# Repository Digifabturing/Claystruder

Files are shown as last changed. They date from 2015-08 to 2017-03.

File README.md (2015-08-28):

# Claystruder

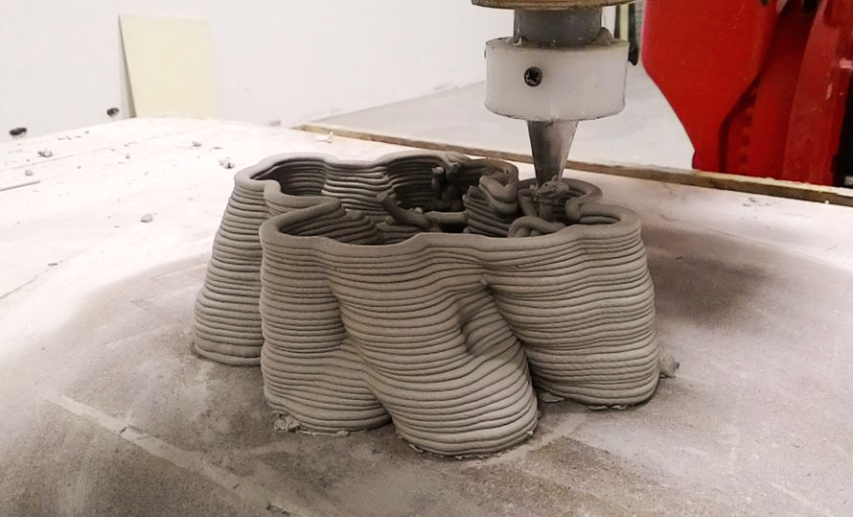
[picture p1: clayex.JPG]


### Introduction:

The Claystruder project is part of the digifabTuring research, that are a research
cluster focused about digital fabrication + robotic automation and material research
applied in the field of architecture, interaction design and art.
digifabTuring rises from a collaboration between several partners: Fablab Torino,
Officine Arduino, Co-de-iT with COMAU and Toolbox Coworking.

We have developed an hybrid extruder system to print clay and other dough, that we use
with a COMAU NJ60 anthropomorphic arm.
The pneumatic system move the clay to the screw conveyor to print the material.

We have developed a Grasshopper definition to, that allow the user to generate the
printing toolpath in a simple way. The definition was created to:
- transform toolpath curves into data to control a 6 axis robot movements
- convert the data to COMAU robot programming language PDL2
- do a raw preliminary check of possible collisions between the robot and
  surrounding objects (basically the work area plane)
- control a clay extruder and simulate its material extrusion path and deposition

### The CODE process:

The Blue part is collecting all the grasshopper settings in order to control the entire process, so please check & set it carefully !!

0. here you move your geometries (toolpath curves) to the robot work area
1. toolpath subdivision: the robot requires points (planes) in order to move. You can set the resolution of its movements adjusting the lenght of the curves subdivisions.
2. retraction: the GH def customizes the height of the movements between different extrusions on the same layer. it's possible also to squeeze a little the material in order to cut it before the next extrusion
3. the GH definition, since is set to control a material extrusion, is set to have the tool working always vertical, but you can change the toolpath planes
4. here you can customize your Robot data: base points and mesh geometry in order to calculate the rotations and simulate the robot movements. Since the IK core is based on the Daniel Piker Lobster Grasshopper definition you can check here the Lobster_IK.pdf document http://www.grasshopper3d.com/group/lobster to properly set your robot data.
5. set the tool offset
6. simulate the tool mesh shape
7. calculate the inverse kinematics in order to get all the single motors rotations for each toolpath points. The IK solver component is the Lobster one developed by Daniel Piker.
8. here you can find two clash controls. The first one is a check of all the 6 axis rotations into the allowed rotation domains of your robot. If some rotation is bigger than the allowed one you will get an error message, its location in the rotations list and you CAN'T save the final file.  The second one is a raw test of the wrist robot position and the work area plane position. if the wrist Z position is under the working area you will get an error message
9. here you can manipulate the robot speed during the extrusion (or whatever work you are doing with it). A specific speed will be assigned to the robot for every specific toolpath point.
10. here you can compose the specific robot code. We are working with a 'COMAU NJ 60' 6 axis robot and its PDL2 programming language but you can customize this part of the code at your specific needs.
11. finally ... you can export your code !! enjoy it

A project of [digifabTuring](http://digifabturing.tumblr.com/)
Developed by:

  Stefano Paradiso from [FablabTorino](http://fablabtorino.org/)/[Officine Arduino](http://local.arduino.cc/torino/), Andrea Graziano, Bruno Demasi,
  Alessio Erioli, Tommaso Casucci, Michele Semeghini from [Co-de-iT](http://www.co-de-it.com/)

In the definition we are using the Lobster reloaded component to calculate the
Inverse Kinematics, the component was written by [Daniel Piker](http://www.grasshopper3d.com/group/lobster/forum/topics/lobster-reloaded).

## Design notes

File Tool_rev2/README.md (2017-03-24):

### BOM

- n.1 meter Polypropylene Pipe diameter 32mm
- n.1 Polypropylene Tee 45° diameter 32mm
- n.1 Spiral Dowel Pins For Thermal Insulation
- n.1 Pneumatic container DIY - tank model in the 3D model
- n...Some metallic sac à poche nozzles of different diameter (http://www.amazon.com/Norpro-Piece-Cake-Decorating-Set/dp/B000LNQ73K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)
- n.1 piece of birch plywood
- n.1 Power motor - check datasheet motor file

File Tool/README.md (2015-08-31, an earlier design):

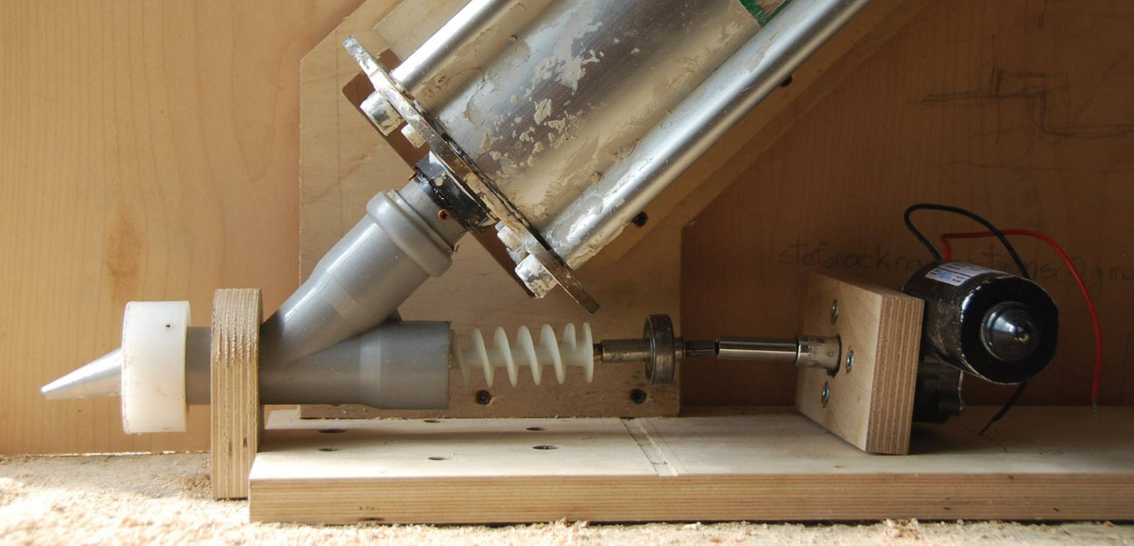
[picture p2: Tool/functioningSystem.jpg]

functioning system

###BOM

- n.1 meter Polypropylene Pipe diameter 32mm
- n.1 Polypropylene Tee 45° diameter 32mm
- n.1 Spiral Dowel Pins For Thermal Insulation (http://www.amazon.co.uk/Spiral-Dowel-Pins-Thermal-Insulation/dp/B00BHTP8S2)
- n.1 Bearing 29mm diameter
- n.1 Pneumatic container - ROLLYCARP GUN BAIT(http://www.rollycarp.it/inglese/gun-bait-support/)
- n...Some metallic sac à poche nozzles of different diameter (http://www.amazon.com/Norpro-Piece-Cake-Decorating-Set/dp/B000LNQ73K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)
- n.1 piece of 70x50 cm birch plywood
- n.1 Power window motor
- n.1 Arduino Leonardo
- n.1 Mosfet IRF530 or similar
- n.1 rs232 - ttl converter (http://users.ntua.gr/dpiperid/MyWebPage/Contructions/converters/rs232tottlEN.htm)

### Serial port connection
the arduino Leonardo is connected to the COMAU robot NJ60 through serial communication,
for that we have used the rs232 to ttl converter. You will connect the RX from the converter
to the arduino TX(PIN1) and the TX from the converter to the arduino RX(PIN0), and
the GND from the converter to the arduino GND.

### Motor connection
We will use a MOSFET to control the motor, in this way we can control the motor speed to.
For the connection and information about motor and MOSFET you can follow this [tutorial](http://bildr.org/2012/03/rfp30n06le-arduino/).

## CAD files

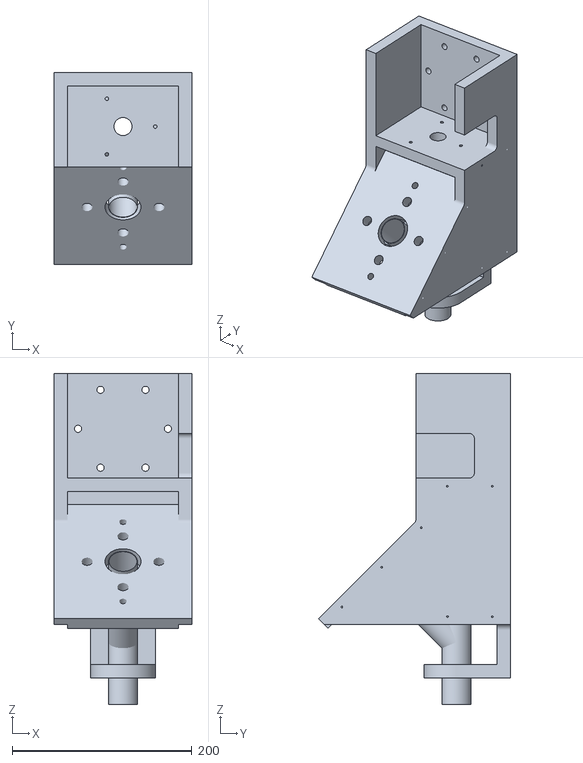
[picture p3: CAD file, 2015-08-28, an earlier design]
Tool/3Dmodel_0.1.stl
153.0 x 213.3 x 368.2

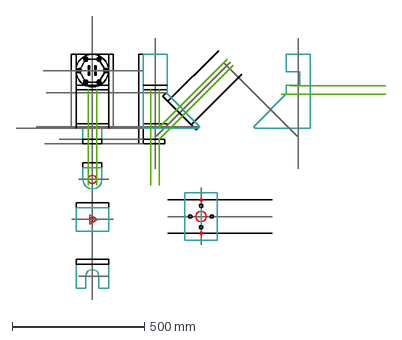
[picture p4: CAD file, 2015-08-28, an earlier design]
Tool/technicalDrawings_0.1.dxf
1393.6 x 1072.0 mm

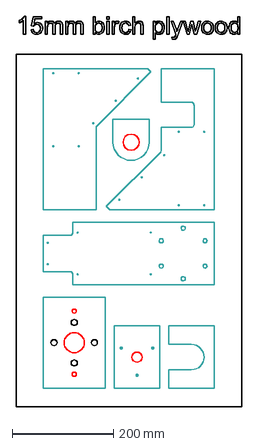
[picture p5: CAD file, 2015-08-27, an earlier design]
Tool/CNC_cutting_file_0.1.dxf
445.7 x 771.9 mm

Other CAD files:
Tool_rev2/CNC_cutting_file_0.2.dxf
Tool/CNC_cutting_file_0.1.3dm

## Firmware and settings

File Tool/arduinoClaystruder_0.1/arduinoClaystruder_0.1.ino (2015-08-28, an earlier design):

String readRobot;
//motor pin mosfet
int motorPin = 11;
char c;

void setup() {

  Serial.begin(115200);
  Serial1.begin(115200);
  delay(200);
  while (!Serial) {
    ;
  }
  Serial.println("ready");
}

void loop() {

  while (Serial1.available()) {
    c = Serial1.read();  //gets char from COMAU robot
    readRobot = String(c); //convert char in string
    Serial.println(readRobot); //print the value
    delay(1);  //slow down the looping
  }

  if (readRobot.length() > 0) {
    //Serial.println(readRobot);  //debug
    analogWrite(motorPin, int(c)); //set the motor speed
    readRobot = ""; //empty for next input
  }
}
